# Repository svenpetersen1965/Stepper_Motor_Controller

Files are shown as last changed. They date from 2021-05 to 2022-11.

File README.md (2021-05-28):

# Stepper Motor Controller
The purpose of this project is top provide an Arduino (Pro Micro) based stepper motor controller with two output channels, rotary encoder, LCD display and an RS-232 interface (beside the serial via USB interface of the Pro Micro) with a 3D printed case and a software framework (Arduino Sketch) suitable for many purposes.

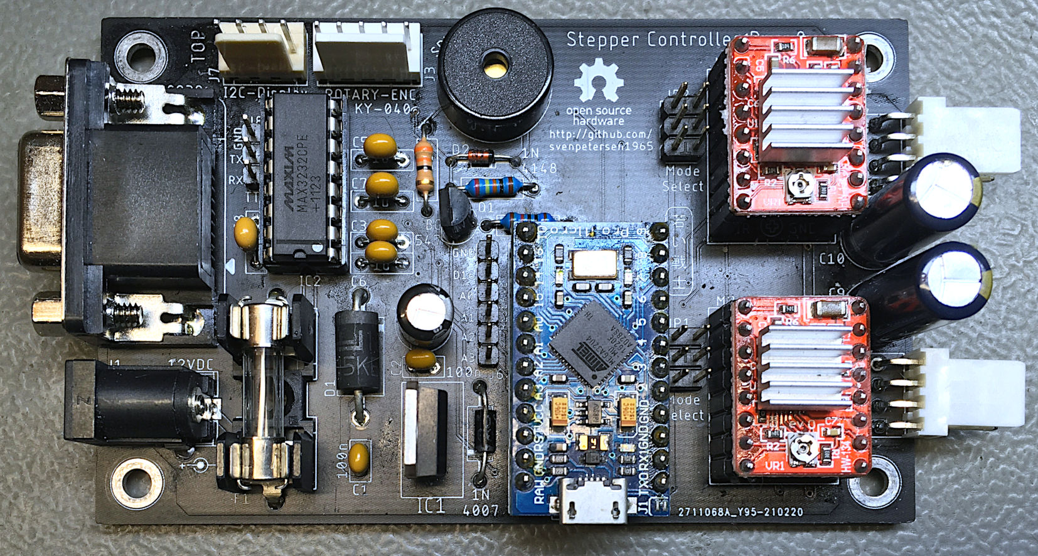
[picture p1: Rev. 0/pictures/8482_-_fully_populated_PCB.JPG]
PCB


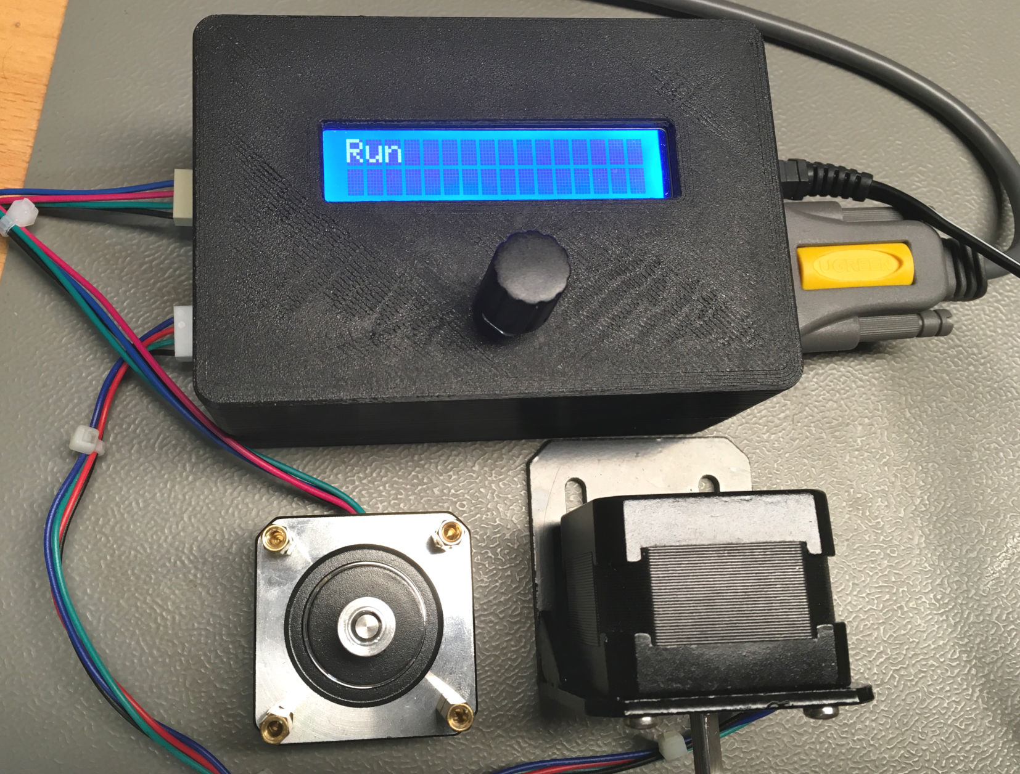
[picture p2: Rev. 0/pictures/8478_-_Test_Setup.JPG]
Setup


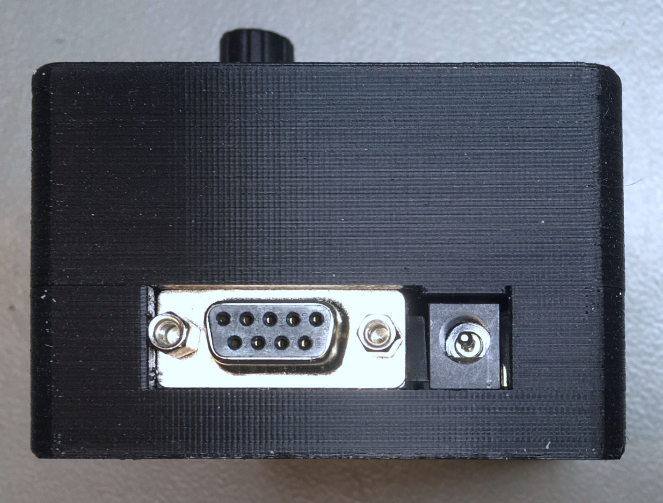
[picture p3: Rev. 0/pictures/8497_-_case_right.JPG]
Power and RS-232


The 3D printed case provides different versions of the top and bottom shells. 

In case you are not experienced with cable making, you might want to read the <a href="http://tech.guitarsite.de/cable_making.html">essay about this topic on my website</a>.

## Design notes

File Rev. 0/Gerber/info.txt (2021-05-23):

      
       Board: Stepper_Controller
       Rev.:  0
  
       Files:
       ======
  
       All Gerber files are generated in extended gerber format (RS274X)
       *.TOP        : Film top copper
       *.BOT        :  -"- bottom copper
       *.STC        :  -"- top soldermask 
       *.STS        :  -"- bottom soldermask
       *.PLC        :  -"- silk screen top
       *.PLC        :  -"- silk screen top
       *.DK         : Drills plated Through (Excellon)
       *.NDK        : Drills not plated Through (Excellon)
       *.OUT        : Board outline

       Board Size:
       ===========
       Length     :   99.0 mm
       Width      :   62.0 mm
       Thickness  :   1.6 mm
       Material   :   FR 4
       Copper     :   35 um
       Surface    :   HASL
       
       Remarks:
       ========
       minimum drill: 0.35mm
       minimum width: 8 mil
       minimum distance: 6 mil

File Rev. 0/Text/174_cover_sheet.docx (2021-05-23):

Project Documentation

Stepper Motor Controller

Project number: 174

Revision: 0

Date: 15.05.2021

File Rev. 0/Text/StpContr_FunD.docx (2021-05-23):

Stepper Motor Controller Rev. 0

Functional Description

J1 is the power supply connector. F1 is the 5x20mm fuse, which might require to be adjusted to the application/stepper motors. D1 is a TVS diode for transient (0voltage spike) suppression. It is calculated for a 12V supply voltage. In case a different supply voltage is desired, a different TVS diode has to be selected.

IC1 is shown as a Traco TRS2-2450 DC/DC converter. Since this is pin compatible to the standard linear regulators, a 7805 can be populated instead of the DC/DC converter, which might be required for higher supply voltages (e.G. 24V for 24V stepper motors).

D3 is a protection when switching off the Stepper motor controller. It helps that the output voltage of IC1 is not much higher than the input voltage (due to charged capacitors).

M1 is a Pro Micro, a popular Atmel Atmega32U4 based micro processor module, which is compatible to the Arduino Leonardo. To send the program/script to the Pro Micro, the USB-B micro connector has to be connected to the PC, the Arduino IDE software is running, the Arduino Leonardo is selected and the proper COM-Port.

IC2 is the level translator for RS-232 (the logic levels of RS-232 are about +/-10V with the MAX232. C3, C5, C6 and C7 are part of the charge pump for generating the required voltages for the IC2. J2 is the RS-232 jack. CTS and RTS are connected as well as DTR, DSR and DCD.

J8 can be used to repurpose the RX and TX pins or for spying the serial traffic at TTL level.

J6 is a pin header for the unused I/O pins of M1. It usually does not require to be populated.

The circuit around Q1 serves as a buzzer amplifier/protection circuit. Actually, an IO-Pin of M1 could drive the buzzer, but the buzzer can act as a high voltage spike generator on a mechanical impact. Thus, the circuit. R1 is the base resistor of Q1, R2 is for current limiting, D2 is kind of a free-wheeling diode, that helps to prevent reverse voltages.

M2 and M3 are the Allegro A4988 based stepper drivers. M2 is for Channel A/Stepper 1 and M3 for Channel B/Stepper 2. C9 and C10 are the buffer capacitors for VMOT, the +12V supply voltage for the stepper motors. JP1 and JP2 configure the micro step mode. All jumpers open mean “full step”. An open jumper is interpreted as a LOW signale by the A4988.

There is one common Enable Signal () for both stepper motors. In case it is LOW, the stepper motors are active and the axis cannot be moved manually. It performs steps in this mode. In case is HIGH, no current flows through the stepper windings and the axis can be moved manually (at least, if the stepper does not have a gear).

J7 is a connector for the I²C-Bus. Usually, a display is connected. Since the I²C is a bus, additional I²C devices can be connected.

J3 is a connector for the rotary encoder. A KY-040 module, which is pretty wide spread and unexpensive can be connected here.

StpContr_FunD.docx 23.05.2021 16:36 Drafted by Sven Petersen Page 2 of 2 Doc.-No.: 174-6-02-00

StpContr_FunD.docx 23.05.2021 16:36 Drafted by Sven Petersen Page 1 of 1 Doc.-No.: 000-6-00-00

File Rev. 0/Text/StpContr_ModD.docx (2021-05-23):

Stepper Motor Controller Rev. 0

Module Description

# Introduction

The Board is a multi-purpose stepper motor controller based on a Pro Micro (Arduino) and up to two (Allegro) A4988 stepper motor driver. The power supply of +12V (basic configuration) is provided via a barrel connector.

The user interface consists of an I²C display, a rotary encoded with integrated button switch and a piezo buzzer. The connectivity is either an RS232 serial interface or the USB serial interface of the Pro Micro.

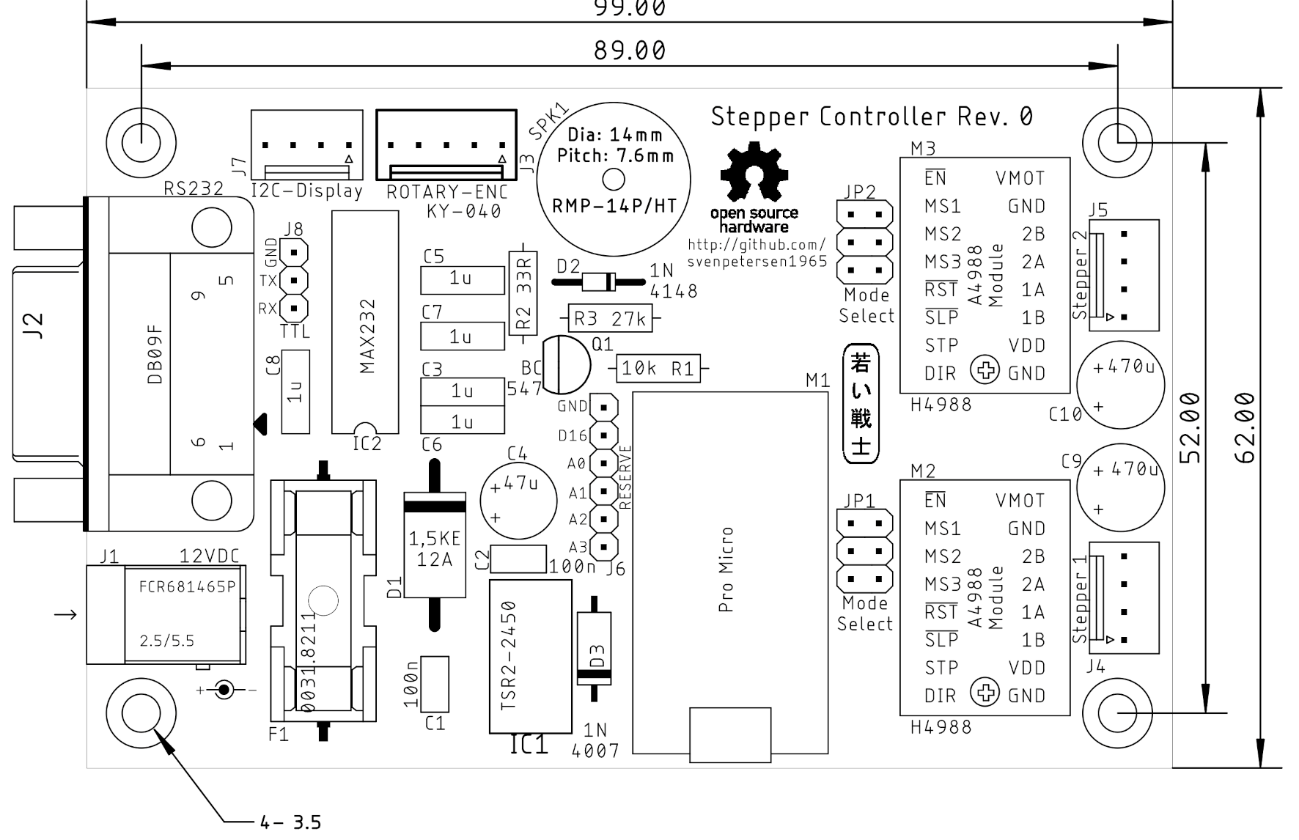
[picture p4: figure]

Figure 1: Dimensions of the Stepper Motor Controller

# Hardware

## The Pro Micro

The Pro Micro is an Arduino Leonardo (Software) compatible, Atmel ATmega32u4-based microprocessor module with 12 digital GPIO pins, 4 analog inputs (which can be used as digital I/Os as well), 32kB Flash, 2.5 kB RAM, 1kB EEPROM and a clock rate of 16MHz and a supply voltage of 5V (3.3V variants with 8MHz are available, but not suitable for this project).

## The A4988 Stepper Driver

The stepper drivers are widely available as modules from Ebay, AliExpress and other online shopping platforms (search term “A4988”). They are based on the Allegro A4988 chip. This chip has five (hardware) selectable step modes: full steps, 1/2, 1/4, 1/8 and 1/16 micro steps. The digital supply voltage is either 5V (used) or 3.3V, the stepper motor supply voltage is up to 35V (12V are used in this projects) and is capable to drive up to 2A.

The micro step mode is selected via jumpers (JP1 for Stepper 1/Channel A and JP2 for Stepper 2/Channel B).

The stepper drivers are controlled by three digital signals:

1. /EN: Enable, active low
2. STEP pulse input
3. DIR direction

The Enable signal /EN needs to be low to activate the driver. A HIGH level will deactivate the drivers. No current flows through the step motor windings, they can be moved freely, stepping will not be executed. The /EN signal of both stepper controllers are interconnected.

A HIGH pulse on the STEP input will result in one (micro) step of the motor in the direction determined by the DIR pin (HIGH = clockwise, LOW = counterclockwise).

Both, the STEP and the DIR signals are separate for each of the two stepper drivers.

There is a small potentiometer on each stepper driver module, which is for adjusting the motor current. To provide approximately equal micro steps, this potentiometer has to be adjusted properly. An adjustment based on the acoustic impression while the stepper motor is running is sufficient for most purposes. It also determines the “hold current”, which influences the supply current and the momentum, the stepper motor is capable to hold.

## The Power Supply

The power supply is connected to a 5mm/2.1mm barrel connector (+12V at the inner contact). The supply voltage is fused and over voltage protected, it is connected to the stepper motor supply pin (VMOT) of the stepper driver. Hence, it is possible to modify the PCB in a way, that 24V stepper motors can be driven. For this purpose, the fuse and the TVS diode D1 need to be modified.

The 5V for supplying the Pro Micro, the digital side of the stepper driver, the display, the buzzer and the rotary encoder, is generated from the input supply voltage. For a +12V supply, a simple linear 7805 voltage regulator is sufficient. The PCB provides the space to install a DC/DC converter (Traco TSR2-2450) instead, that might be required for powering the PCB with a higher supply voltage.

## The Display

The display is connected to the I²C bus via a four-pin connector, which also provides a +5V pin for power supply. This will operate with the wide spread 16 columns/two lines or 20 columns/four lines LCD displays (I²C).

It is of course possible to connect an OLED-display with 5V supply voltage with a suitable software running on the Pro Micro.

## The Rotary Encoder

Rotary encoders with an integrated push button are usually pretty common and suitable for a menu-based mode selection and parameter entry. A widely available rotary encoder module (with on-board pull-up resistors) is the KX-040. The connector for the rotary encoder is adapted to this module. In case, a rotary encoder is not required for the supplication, the pins can be repurposed.

## The Piezo Buzzer

The purpose of the piezo buzzer is providing acoustic feedback or a warning signal for the user. Since piezo elements can produce some nasty voltage spikes when they get bent or beaten, the buzzer is not directly connected to the processor pin, but there is a protection circuit with a transistor and a diode.

## Serial RS-232-Interface

The Pro Micro provides a virtual serial interface via USB for communication and also a real serial interface with RX/TX pins. An RS-232 level driver is integrated on this board. The connector is the D-Sub 9, female, so the stepper controller is a DCE (Data Communication Equipment) like a modem. It connects to a computer (or other DTE = Data Terminal Equipment) via a 1:1 serial cable. Some feedbacks are provided (RTS-DTS and DTR-DRS-DCD).

# Programming

The Stepper Motor Controller (actually the Pro Micro) can be programmed with the Arduino IDE. The following chapters describe the source code of stepper_framework.ino, which does not do anything useful, except testing the hardware, nevertheless, this can be a framework to customized applications.

## Pin Configuration

The pin configuration looks like this:

Pin | Direction | Signal | Purpose
D0 | out | TX | RS-232 Interface serial output
D1 | in | RX | RS-232 Interface serial input
D2 | - | SDA | I²C SDA signal
D3 | - | SCL | I²C SCL signal
D4 | in | ROT_SW | Rotary Encoder Switch
D5 | in | ROT_DATA | Rotary Encoder Data (actually output A)
D6 | out | STP_IN | Stepper driver 1 (Channel A) pulse input
D7 | out | STP_DIR | Stepper driver 1 (Channel A) direction input
D8 | input | ROT_CLK | Rotary Encoder Clock (actually output B)
D9 | out | SND_OUT | Output to the piezo buzzer
D10 | out | | Stepper Enable (active low) for both stepper drivers
D14 | out | STP2_IN | Stepper driver 2 (Channel B) pulse input
D15 | out | STP2_DIR | Stepper driver 2 (Channel B) direction input
D16 | - | D16 | Reserved GPIO
A0 | - | A0 | Reserved (analog) GPIO
A1 | - | A1 | Reserved (analog) GPIO
A2 | - | A2 | Reserved (analog) GPIO
A3 | - | A3 | Reserved (analog) GPIO

## Stepper Driver

The pins are defined like this:

#define step1 6 // stepper 1 step

#define dir1 7 // stepper 1 direction

#define step2 14 // stepper 2 step

#define dir2 15 // stepper 2 direction

#define nstpena 10 // enable both steppers (active low)

Pin initialization:

// setup stepper controller

digitalWrite( step1, LOW ); // LOW -> Step Signal

digitalWrite( dir1, st_direction ); // default direction

digitalWrite( step2, LOW ); // LOW -> Step Signal

digitalWrite( dir2, st_direction ); // default direction

digitalWrite( nstpena, HIGH ); // disable stepper by setting the enable pin HIGH

pinMode( step1, OUTPUT ); // step1 is an output

pinMode( dir1, OUTPUT ); // dir1 is an output

pinMode( step2, OUTPUT ); // step1 is an output

pinMode( dir2, OUTPUT ); // dir1 is an output

pinMode( nstpena, OUTPUT ); // nstpena is an output, that is the enable output for both stepper controllers

Previously, the direction was set to the desired value:

#define step_cw HIGH // for clockwise, the direction pin is HIGH

#define step_ccw LOW // for counterclockwise, the direction pin is LOW

[…]

digitalWrite( dir1, step_cw );

To switch on the stepper driver output and perform a step, the stepper drivers need to be enabled by setting the enable input LOW:

digitalWrite( nstpena, LOW ); // enable stepper controller

Setting the direction:

#define step_cw HIGH // for clockwise, the direction pin is HIGH

#define step_ccw LOW // for counterclockwise, the direction pin is LOW

[…]

digitalWrite( dir1, step_cw );

One step is performed like this:

void makeStepA( void ) { // make a step on motor A

digitalWrite( step1, HIGH );

delayMicroseconds( puls_width );

digitalWrite( step1, LOW );

}

## The Piezo Buzzer

Pin definition:

#define buzzer 9 // buzzer

Pin initialization:

pinMode( buzzer, OUTPUT ); // the buzzer is an output

Using the piezo buzzer:

// beep "hello"

tone( buzzer, 4000 ); // 1kz sound on buzzer

delay( 1000 ); // for 1 second

noTone( buzzer );

## The LCD-Display

The I²C LDC Display requires including two libraries:

#include <Wire.h> // import Wire library

#include <LiquidCrystal_I2C.h> // import LiquidCrystal_I2C library

The initialization includes the I²C address, the number of column and the number of lines. Here a 16x2 display is used.

LiquidCrystal_I2C lcd(0x27, 16, 2); // define the lcd display (i²c address

// 0x27, 16 columns, 2 lines

## The Timer 1 Interrupt

The Timer 1 interrupt is actually the heartbeat of the software. This interrupt occurs periodically and the so called ISR (Interrupt Service Routine) is executed. The cycle duration/periodicity depends on the setup (parameters) of Timer 1.

Note: Many beginners and intermediate programmers are afraid of using interrupts. This fear is actually not required! The ISR can be imagined as a sub routine, that is executed on interrupt, which is not noticed by the main program and can happen at any time. It is a task, that is executed in the background. The communication between the main program and the ISR is accomplished with variables.

There are two main rules for the Interrupt Service Routine:

1. Keep it simple (the execution times should not be too long)
2. The variables, which need to be seen by the main program and the ISR need to be declared as “volatile” to disable compiler optimizations, that might want to store such a variable in a register. The main program will look up the value by loading the register, while the ISR has changed the value in memory.

Rule number 2 is violated quite often, which leads to an unreliable/unpredictable processing of the events, that cause the interrupt.

The declaration of a “volatile” variable looks like this:

volatile boolean step_flag = 0;

It works with all basic variable types. step_flag is set by the ISR (after a defines time has elapsed), the main loop is checking if step_flag is set, if so, a step is performed and step_flag is then reset by the main loop. That simple!

The setup of the timer interrupt looks like this:

/* ==================== TIMER 1 setup ======================= */

// Interrupt every 0.000496 sec (= 2016.13Hz)

// prescaler = 256

// Compare Match Register = 30

cli(); // disable interrupts

// reset timer1

TCCR1A = 0; // set TCCR1A register to 0

TCCR1B = 0; // set TCCR1B register to 0

TCNT1 = 0; // reset counter value

OCR1A = 30; // set compare match register of timer 1

TCCR1B |= (1 << CS12); // 1:256 pre-scaling for timer1

TCCR1B |= (1 << WGM12); // turn on CTC mode

TIMSK1 |= (1 << OCIE1A); // enable timer compare interrupt

sei(); // allow interrupts

The clock frequency is 16MHz for the Pro Micro (5V version). This frequency is divided by the prescaler (here 256). The result is a frequency of 62.5kHz, which is the input frequency of timer 1. The compare/match register is set to 30. So, timer 1 counts from 0 to 30 before the timer interrupt occurs. That are 31 counts.

T_(TIMER1) =(prescaler ∙(OCR1A+1))/(16MHz)=(256∙(30+1))/(16MHz)=0.496msec

CTC mode means the described cyclic counting mode.

The prescaler has a just few specific modes.

CS12 | CS11 | CS10 | Prescaler
0 | 0 | 1 | 1:1 (no prescaler)
0 | 1 | 0 | 1:8
0 | 1 | 1 | 1:64
1 | 0 | 0 | 1:256
1 | 0 | 1 | 1:1024

A recommended reading about the timer interrupts is: https://www.simsso.de/?type=arduino/timer-interrupts

This website includes a parameter calculator.

## The Interrupt Service Routine

The ISR includes the timing for the steps and the processing of the rotary encoder signals.

ISR(TIMER1_COMPA_vect) { // function which will be called
// when an interrupt occurs at timer 1

// ========= every one second ========

if (++t1_ticks == t1_ticks_sec) { // set tick_1s every 2016 IRQ cycles (every 1 second)

tick_1s = 1;

t1_ticks = 0; // reset the tick counter

}

// === count the time before the next stepper step ===

if (++step_ticks == step_duration) {

step_flag = 1;

step_ticks = 0;

}

// ============== rotary encoder =====================

rot_read = digitalRead( rot_clk );

if ( rot_read != rot_clk_status) { // is rot_clk different for
// <debounce> cycles?

if (--rot_clk_debounce == 0) {

rot_clk_status = rot_read; // if yes: change status

}

}

else {

rot_clk_debounce = debounce; // if it is equal -> reset
// the debounce counter

}

if (rot_clk_status != rot_clk_status_old) { // did a status change
// occur?

if (rot_clk_status == LOW) { // is it a falling edge?

if (digitalRead( rot_data ) == LOW) { // yes: set the roraty value
//according to rot_data

rot_value--; // LOW -> CCW

}

else {

rot_value++; // HIGH -> CW

}

}

rot_clk_status_old = rot_clk_status; // update old status

}

rot_read = digitalRead( rot_sw ); // read rot switch

if ( rot_read != rot_sw_status) { // is rot_sw different for
// <debounce> cycles?

if (--rot_sw_debounce == 0) {

rot_sw_status = rot_read; // if yes: change status

}

}

else {

rot_sw_debounce = debounce; // if it is equal -> reset
// the debounce counter

}

if (rot_sw_status != rot_sw_status_old) { // did a status change
// occur?

if (rot_sw_status == LOW) { // is it a falling
// edge?

rot_button = true; // set switch semaphore

}

rot_sw_status_old = rot_sw_status; // update old status

}

}

The ISR consists of three parts:

1. A 1sec tick
2. A tick per desired (micro) step
3. The rotary encoder debouncing and processing (refer to the following chapter)

The 1sec tick is setting the “flag” tick_1s to 1. This flag can be monitored by the main loop. The main loop has to reset this flag after “detection”. This is called a “semaphore”, which means a structure, that is used for signaling between different processes (here it is the ISR and the main loop).

step_flag is the semaphore, which signalizes the main loop, that the time for the next set has elapsed. The main loop has to reset this flag after detection, as well.

## The Rotary Encoder

The rotary encoder part of the ISR (refer to the previous chapter) is supervising the “clock” and the “switch” signals.

The rotary encoded used here has mechanic contacts. Those are bouncing, when they change state. That means they are quickly oscillating for a while, before they finally settle. To detect a valid status change of the rotary encoder, the supervised signal has to stay the same for the debouncing period of time, which is determined be the constant debounce (a certain number of ISR cycles).

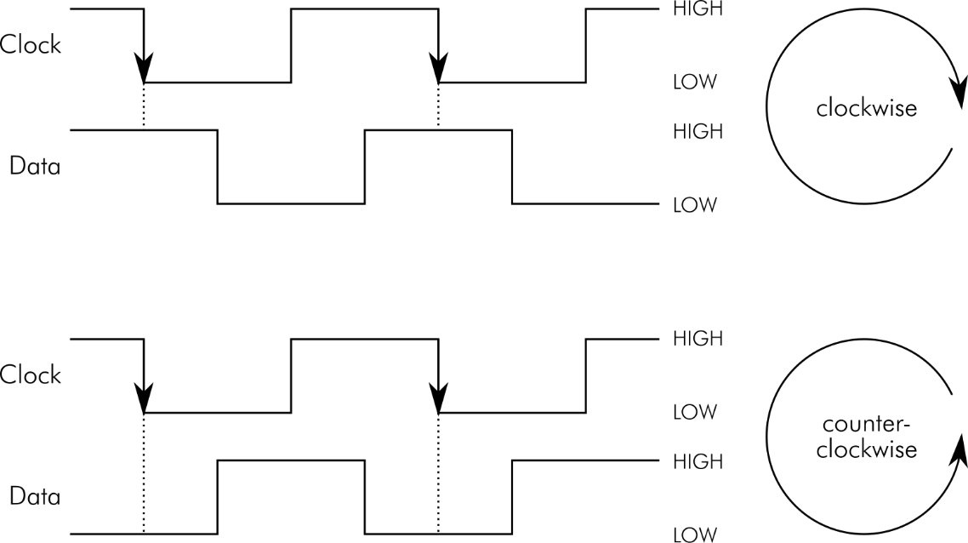
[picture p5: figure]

Figure 2: Operation of the rotary encoder

The relation between the clock and the data signal of the rotary encoder depends on the rotation direction. It is plus or minus a quarter period (that is +/- 90°, 360° is a complete period).

The direction can be detected by reading the data signal right after the falling edge of clock. This is accurate enough for a rotary encoder serving as an input device.

The interrupt service routine (ISR) is detecting a falling edge by comparing the recently read (valid) status of the clock signal (rot_clk_status) and the previously read status (rot_clk_status_old). In case both are different and the present status is LOW, a falling edge is detected. Now, the data signal is read. Depending on the state of the data signal, the variable, that holds the number of rotary encoder clicks (rot_value) is counted up (clockwise turn) or down (counterclockwise turn). rot_value is another semaphore, which is communicating the rotary encoder operation to the main loop.

The status of the rotary encoder’s push button is also monitored by the ISR. Like the clock signal, it has to be debounced. Since the button is a switch to ground (GND), a pushed button shows as reading a LOW state. The (after debouncing) valid state of the button is stored in the semaphore rot_button. The variable is true, if a button push is detected.

Processing the rotary encoder in the main loop is fairly simple. Just the previously mentioned semaphores have to be monitored.

Detecting the button:

lcd.setCursor(14,0);

if (rot_button==true) { // rotary encoder:
// button pushed

rot_button = false; // reset this flag

// after detection

Serial1.print("Button->set (Channel ");

if (stepper == step_cha) {

Serial1.println("A)");

}

else {

Serial1.println("B)");

}

}

Or the direction of rotation:

if (rot_value != 0) {

if (rot_value < 0) {

num_steps = num_steps - 10;

rot_value++;

}

else {

num_steps = num_steps + 10;

rot_value--;

}

lcd.setCursor(7,1);

lcd.print( num_steps );

lcd.print( " " );

Serial1.print( "Steps: " );

Serial1.println( num_steps );

}

Here the number of steps (num_steps) is reduced by 10 on each “click” while rot_value is < 0 (direction = CCW) and increased by 10 while rot_value is > 0 (direction = CW).

## RS-232

Other than the “regular” serial (via USB) interface, this RS-232 is addressed as Serial1 in the Arduino IDE. The programming works like with the first serial interface. The recommended reading is https://www.arduino.cc/reference/en/language/functions/communication/serial/.

The initialization works with

Serial1.begin(9600);// the RS232 interface (RX, TX on pin 0 and 1) is

// Serial1.

This the 9600 bit/s (aka 9600 baud), 8N1 (8 data bits, No parity, 1 stop bit), a very common baud rate and data format.

Sending text via the serial interface is fairly simple:

Serial1.println( "Hello RS-232" ); // say hello

The RS-232 interface is also for receiving commands from a host. To collect this data and later process it (parsing the string = extracting the commands and parameters), some RAM space (a buffer) is allocated. For the parsing, the String functions are required

String recString = ""; // receive command buffer

[…]

recString.reserve(80);

A process, that is executed on every event on the Serial1 (RS-232) interface is

void serialEvent1() {

while (Serial1.available()) { // bytes available on Serial1?

recByte = (char)Serial1.read(); // read it

if (recByte == (char)10) { // is it "new line character"?

recComplete = true; // yes: the line is complete

}

else {

recString += recByte; // no: append character to input string

}

}

}

As long as there is data available on the interface, it is checked, if the data byte (actually a character) is a “Line Feed” (= (char)10 ). The line feed denotes the end of a command string. If so, a semaphore (recComplete) is set true. If it is a different character, this will be appended to the buffer recString.

The parsing of the received string in the main loop looks like this:

if (recComplete) { // a complete command line is received on RS-232

lcd.setCursor(0,1); // position the cursor on the second line

lcd.print( recString ); // print the received string

lcd.print( " " ); // clear the line after that string

recString.toUpperCase(); // convert the line to upper case

// (it is not case sensitive)

syntaxError = false; // reset the Syntax Error flag

if (recString[0] == 'A') { // is the first character an A?

stepper = step_cha; // yes: select Stepper#1 (channel A)

}

else if (recString[0] == 'B') { // is the first character a B?

stepper = step_chb; // yes: select Stepper#2 (channel B)

}

else {

syntaxError = true; // else, the syntax is not correct.

}

if (!syntaxError) { // syntax still correct?

int pos = (int) recString.indexOf(","); // find the first comma ","

if (pos < 1) { // if no comma is found

syntaxError = true; // set the Syntax Error Flag

}

else { // a comma is found:

recString.remove(0,pos+1); // remove the beginning, the comma

// included

num_steps = (int) recString.toInt();// convert the string to

// integer -> num_steps

if (num_steps<0) { // is it a negative number?

num_steps = -num_steps; // yes: make it positive

st_direction = step_ccw; // the direction is counterclockwise

}

else { // no:

st_direction = step_cw; // the direction is clockwise

}

digitalWrite( dir1, st_direction ); // set the direction of both

digitalWrite( dir2, st_direction ); // stepper motors

}

}

if (syntaxError) {

Serial1.println("? SYNTAX ERROR"); // report the syntax error

}

else {

Serial1.print("Execute: Channel "); // report the execution

switch (stepper) {

case step_cha: {

Serial1.print("A, "); // Channel A

break;

}

case step_chb: {

Serial1.print("B, "); // Channel B

break;

}

}

Serial1.print( num_steps ); // and the number of steps

if (st_direction == step_cw) {

Serial1.println(" steps, CW"); // and the direction

}

else {

Serial1.println(" steps, CCW");

}

}

recComplete = false; // reset the semaphore

recString = ""; // reset the recString (receive buffer)

The command line will let the selected stepper motor turn CW or CCW by the sent number of steps.

A proper command line looks like this:

<channel>, <number of steps>

While <channel> is A or B or a or b (it is not case sensitive) and a positive <number of steps> will turn the clockwise and a negative <number of steps> will turn counter clockwise.

## State Machine

The main loop is designed as a (finite-)state machine. This is a very common structure for micro controller software, which is quite useful to know.

Depending on the state, the actions and reactions are different. This (desired) behavior can be depicted in a state diagram (Figure 3).

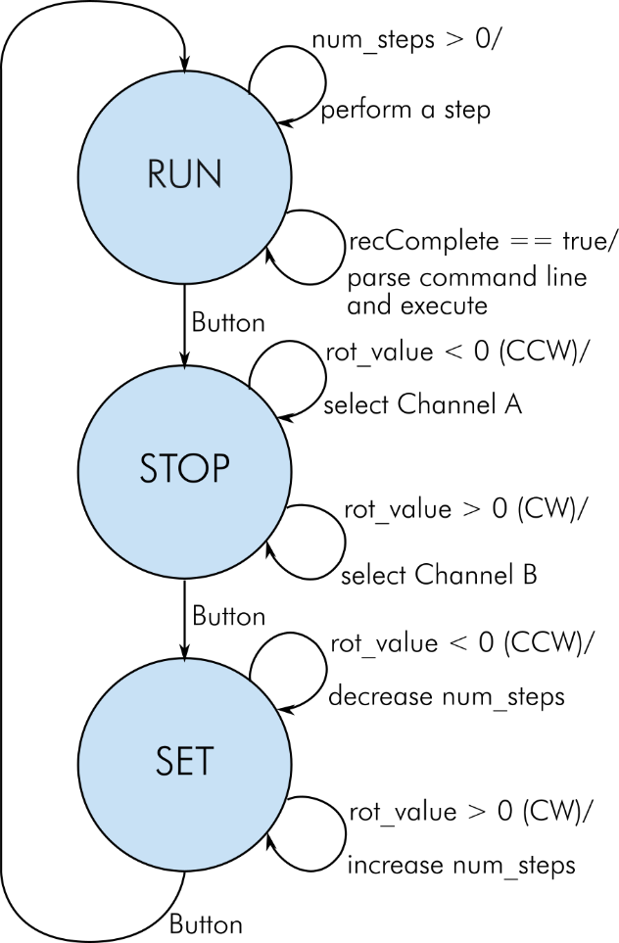
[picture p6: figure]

Figure 3: State diagram

The state machine has three states: RUN, STOP and SET. The states are represented by int values defined like this:

// state machine states

#define sm_stop // assigning a numbers to the state machine states

#define sm_set 1

#define sm_run 2

The state RUN is entered first, it checks, if num_steps is greater 0, if so, it performs a step and decreases num_steps by one.

Also, it checks, if a command line (via RS-232) is complete (recComplete is true), if so, the command line is parsed and executed.

In case the push button of the rotary encoder is pressed, it enters the state STOP.

The state STOP watches the rotary encoder. If it is turned counterclockwise, Stepper channel A is selected, if it is clockwise, Stepper channel B is selected.

If the push button is pushed, the state SET becomes active.

While SET the number of steps to perform next and the direction is adjusted. If the rotary encoder is turned clockwise, the variable num_steps is increased by 10, while counterclockwise, num_steps is increased by 10. A negative number will select counterclockwise for both stepper motors. Pressing the push button will enter the state RUN.

The over-all structure of the state machine is a switch/case construction in the main loop.

switch (state_machine) {

case sm_stop : {

[…]

break;

}

case sm_set : {

[…]

break;

}

case sm_run : {

[…]

break;

}

}

# Connector Pinouts

## J1 - Power Connector

J1 is a 2.5mm/5.5mm barrel jack.

Pin | Signal
Inner | +12VDC
Outer | GND

## J2 – RS-232 Serial Interface

D-Sub, 9 pins, female

Pin | Signal | Note
1 | DCD | Feedback DCD – DTR - DSR
2 | RxD | Output
3 | TxD | Input
4 | DTR | Feedback DCD – DTR – DSR
5 | GND | Ground
6 | DSR | Feedback DCD – DTR – DSR
7 | RTS | Feedback RTS - CTS
8 | CTS | Feedback RTS – CTS
9 | RI | Not connected

## J3 – Rotary Encoder

KF2510 series, 5pin (or Molex P/N 22272051) – vertical header with friction lock. Pinout for KY-040 rotary encoder module.

Pin | Signal | Note
1 | GND
2 | +5V
3 | Switch | Button
4 | Data | Actually, Channel A
5 | Clock | Actually, Channel B

The counterpart of J3 is a crimp housing (also KF2510 series, which is wide spread on Ebay, AliExpress and other online shops) and fitting crimp terminals. Alternatively, Molex P/N 22013047 and crimp terminal P/N 0850-0114 can be used.

## J4, J5 – Stepper Motor Outputs

KF2510 series, 4pin (or Molex P/N 22272041) – vertical header with friction lock or horizontal (90°) Molex P/N 22057048. J4 is Channel A/Stepper 1, J5 is Channel B/Stepper 2.

Pin | Signal | Note
1 | 1B | stepper motor blue cable
2 | 1A | stepper motor red cable
3 | 2A | stepper motor green cable
4 | 2B | stepper motor black cable

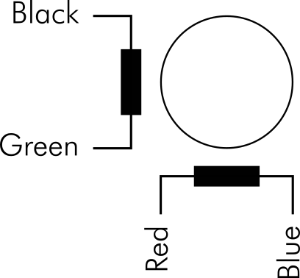
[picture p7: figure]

Figure 4: Windings of the stepper motor/cable colors

## J6 – Reserved I/O-Pins

The free GPIO-Pins of the Pro Micro are connected to a pin header (6 pins, 2.54mm pitch) which does not require to be placed. These pins might serve for connecting sensors/switches/actors

Pin | Signal | Note
1 | GND
2 | D16 | GPIO D16, PCINT2
3 | A0 | Analog input/GPIO
4 | A1 | Analog input/GPIO
5 | A2 | Analog input/GPIO
6 | A3 | Analog input/GPIO

## J7 – I²C/Display Connector

KF2510 series, 4pin (or Molex P/N 22272041) – vertical header with friction lock. Pinout for LCD Displays (16x2) with I²C controller.

Pin | Signal | Note
1 | SCL | I²C clock
2 | SDA | I²C data
3 | +5V
4 | GND

The counterpart of J7 is a crimp housing (also KF2510 series, which is wide spread on Ebay, AliExpress and other online shops) and fitting crimp terminals. Alternatively, Molex P/N 22012041 and crimp terminal P/N 0850-0114 can be used.

## J8 – TX/RX Reserve Header

The TX and RX signals are routed to a pin header (3 pins, 2.54mm), which is not placed, in case it is desired to repurpose them or to watch the data exchange on the serial port/RS-232.

Pin | Signal | Note
1 | GND
2 | TX | serial output, GPIO D1
3 | RX | serial input, GPIO D2

# Jumpers

There are two jumpers, JP1 and JP2. Both serve the setting of the step modes (full step, ½ step, ¼ step, 1/8 step and 1/16 step). JP1 determines the mode of stepper #1/channel A, JP2 does so for stepper#2/channel B).

MS1 / JPx 1-2 | MS2 / JPx 3-4 | MS3 / JPx 5-6 | Mode/micro step resolution
L/open | L/open | L/open | Full Step
H/set | L/open | L/open | Half Step
L/open | H/set | L/open | Quarter Step
H/set | H/set | L/open | Eighth Step
H/set | H/set | H/set | Sixteenth Step

The footprints of the jumpers allow fix solder bridges instead of a pin header and jumper.

# Assembly

## The PCB

The PCB can be fully populated or some not requires parts can be omitted.

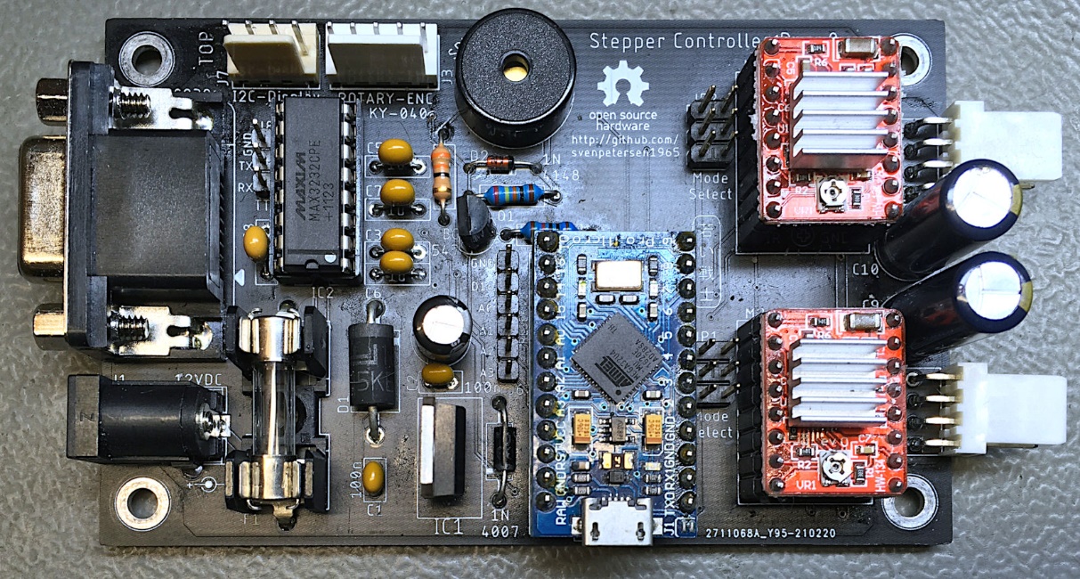
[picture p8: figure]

Figure 5: Fully populated PCB

Requirement | Components
Always populate | J1, F1, C1, C2, C4, D3, M1, M2, C9, J4
2nd stepper controller | M3, C10, J5
Buzzer | R1, R1, R2, R3, D2, SPK1
Display | J7
Rotary Encode | J3
RS-232 | J2, IC2, C3, C5, C6, C7, C8
Micro steps required and jumpered | Channel A: JP1, Channel B: JP2. A fix setting of the jumpers can be accomplished with solder bridges
Do not place (until required) | J6, J8

## Cables

In case the 90° pin headers are used for the stepper motor connection (J4, J5), there are only two cables required:

1. the display cable
2. the rotary encoder cable

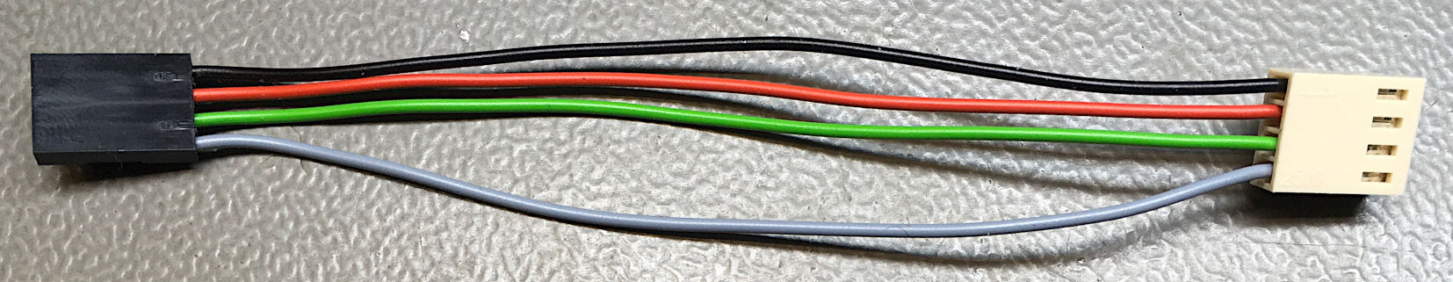
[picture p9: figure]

Figure 6: The display (I²C) cable

This display cable consists of the following components:

Pos. | Qty | Part
1 | 1 | DuPont crimp housing, 4 pins
2 | 4 | DuPont crimp terminals
3 | 14cm | Cable, 0.25mm²/AWG24, black
4 | 14cm | Cable, 0.25mm²/AWG24, red
5 | 14cm | Cable, 0.25mm²/AWG24, green
6 | 14cm | Cable, 0.25mm²/AWG24, grey
7 | 4 | KF2510 crimp terminals
8 | 1 | KF2510 crimp housing, 4 pins

The colors of the cables are a suggestion only.

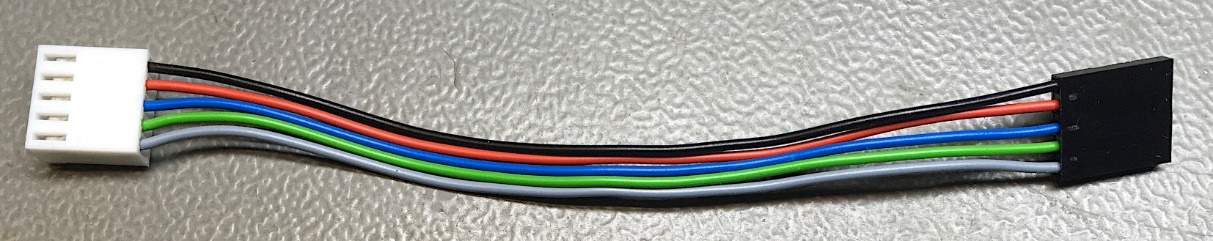
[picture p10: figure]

Figure 7: Rotary encoder cable

This rotary encoder cable consists of the following components:

Pos. | Qty | Part
1 | 1 | DuPont crimp housing, 5 pins
2 | 5 | DuPont crimp terminals
3 | 14cm | Cable, 0.25mm²/AWG24, black
4 | 14cm | Cable, 0.25mm²/AWG24, red
5 | 14cm | Cable, 0.25mm²/AWG24, blue
6 | 14cm | Cable, 0.25mm²/AWG24, green
7 | 14cm | Cable, 0.25mm²/AWG24, grey
8 | 5 | KF2510 crimp terminals
9 | 1 | KF2510 crimp housing, 5 pins

Optionally, a DIN connector can be used for the stepper motor connections.

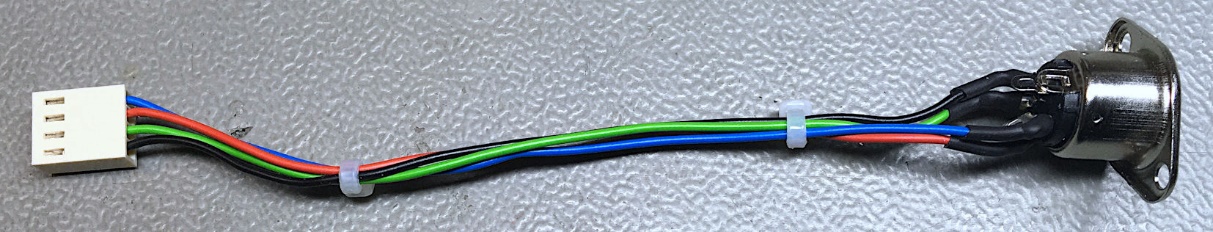
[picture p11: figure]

Figure 8: Stepper cable (internal, optional)

Pos. | Qty | Part
1 | 1 | DIN Jack, 5 pins (e.g. Reichelt MAB 5S)
2 | 14cm | Cable, 0.25mm²/AWG24, black
3 | 14cm | Cable, 0.25mm²/AWG24, green
4 | 14cm | Cable, 0.25mm²/AWG24, red
5 | 14cm | Cable, 0.25mm²/AWG24, blue
6 | 5 | KF2510 crimp terminals
7 | 1 | KF2510 crimp housing, 5 pins
8 | 6cm | Shrinkable sleeve (2.4/1.2)

## 3D Printed Case

It is recommended to use the 3D printed case for this project. It consists of a top and a bottom shell and is constructed in Fusion 360. The STL files for 3D printing are provided as well as the Fusion 360 project.

The display is attached with 4 screws (C2.9x6.5 DIN 7981 recommended). The rotary encoder is attached with the nut included in it. The cables should be connected prior to mounting those components.

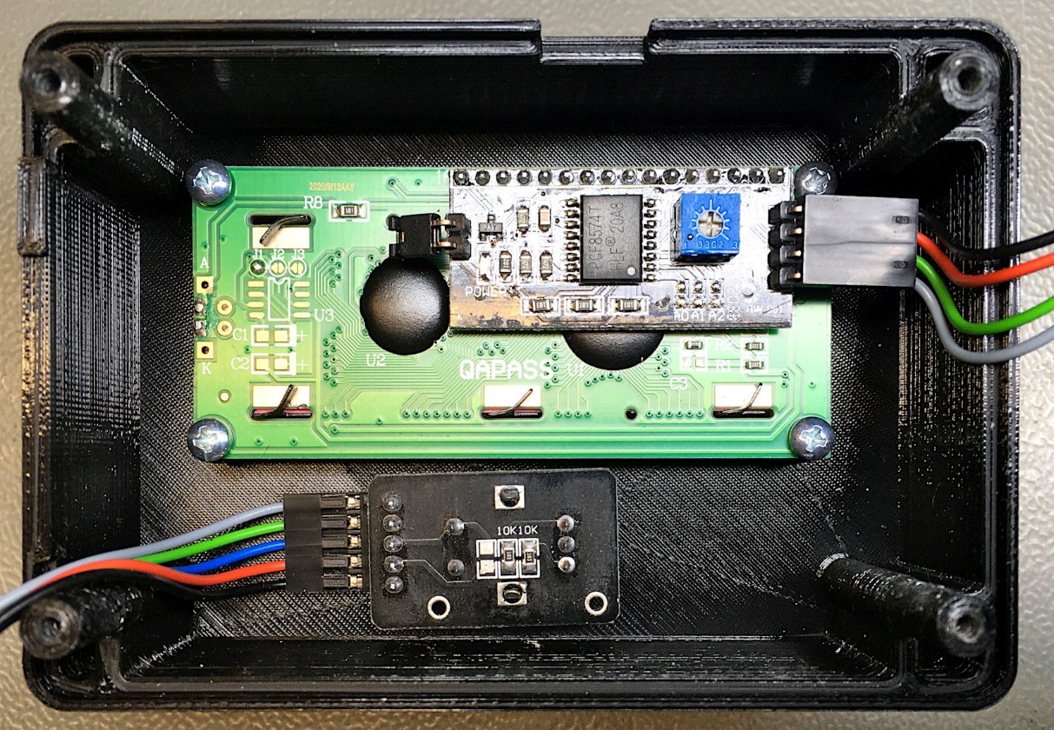
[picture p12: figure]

Figure 9: Top shell with mounted LCD display and rotary encoder KY-040

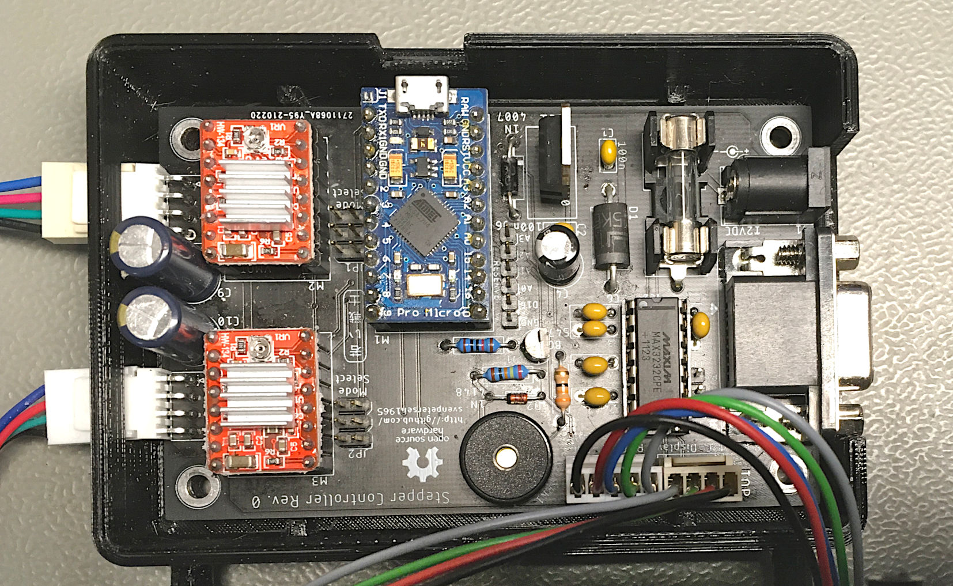
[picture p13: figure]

Figure 10: PCB in bottom shell

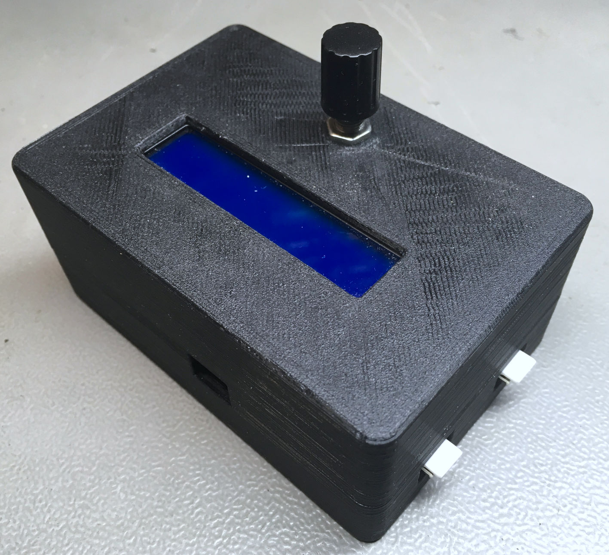
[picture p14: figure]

Figure 11: Case from top, left

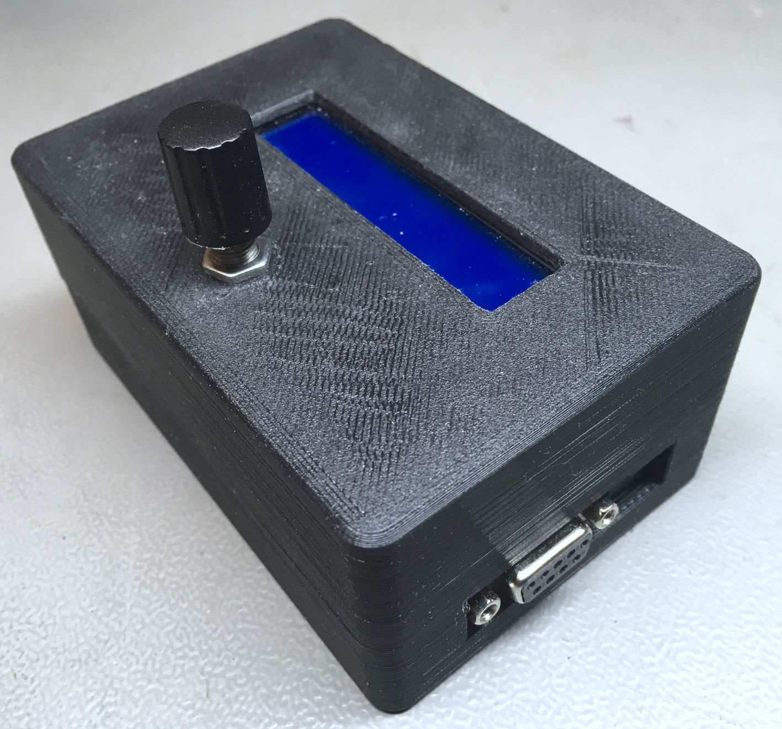
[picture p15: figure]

Figure 12: case from bottom, right

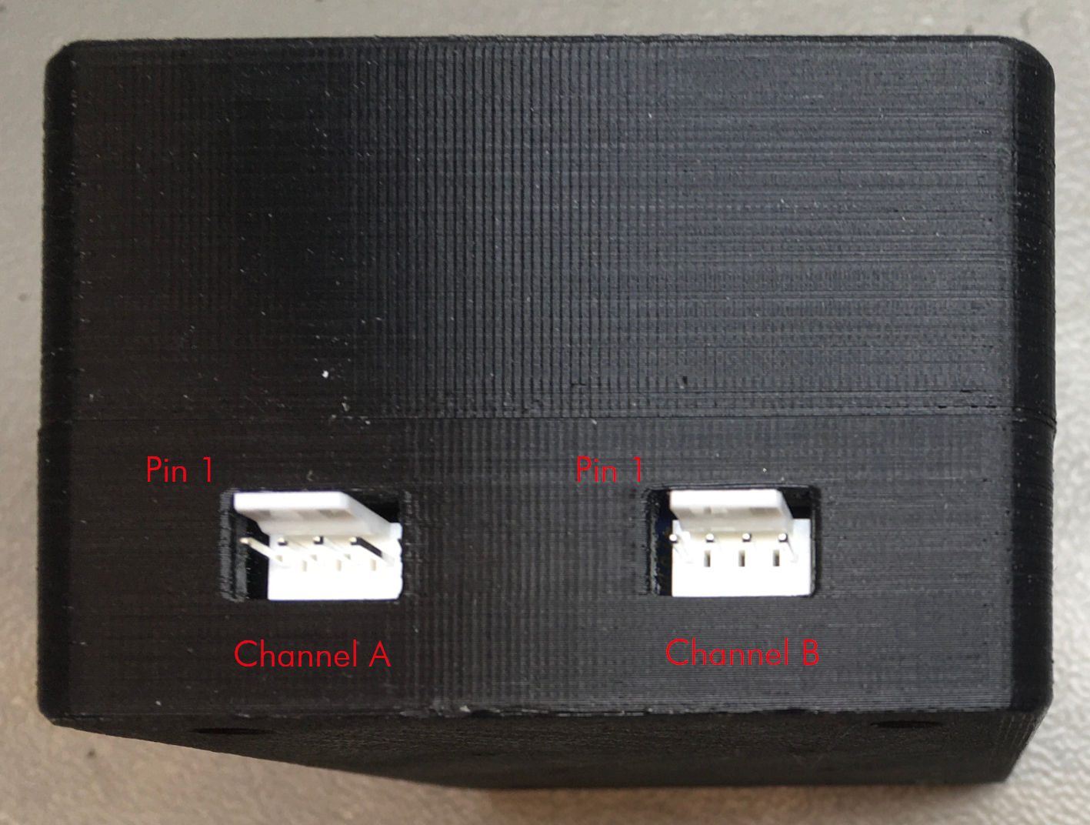
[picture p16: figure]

Figure 13: left side


Figure 14: right side

There are different versions of the top and bottom shell provided. The top shell can have a mounting space for a DIN connector (that could serve as a stepper motor connector), the bottom shell can have the cut outs for the 90° stepper motor connector as shown in Figure 10.

For closing the case, with 4 screws (C2.9x13 DIN 7981 recommended) are required.

# Revision History

## Rev. 0

- Fully functional prototype

StpContr_ModD.docx 23.05.2021 16:35 Drafted by Sven Petersen Page 2 of 2 Doc.-No.: 174-6-01-00

StpContr_ModD.docx 23.05.2021 16:35 Drafted by Sven Petersen Page 1 of 1 Doc.-No.: 000-6-00-00

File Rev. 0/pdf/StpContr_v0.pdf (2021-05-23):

# Project Documentation

## Stepper Motor Controller

## Project number: 174

## Revision: 0

## Date: 15.05.2021

StpContr_ModD.docx | | 23.05.2021 16:35
Drafted by Sven Petersen | Page 1 of 22 | Doc.-No.: 174-6-01-00

### Stepper Motor Controller Rev. 0

### Module Description

Table of Contents

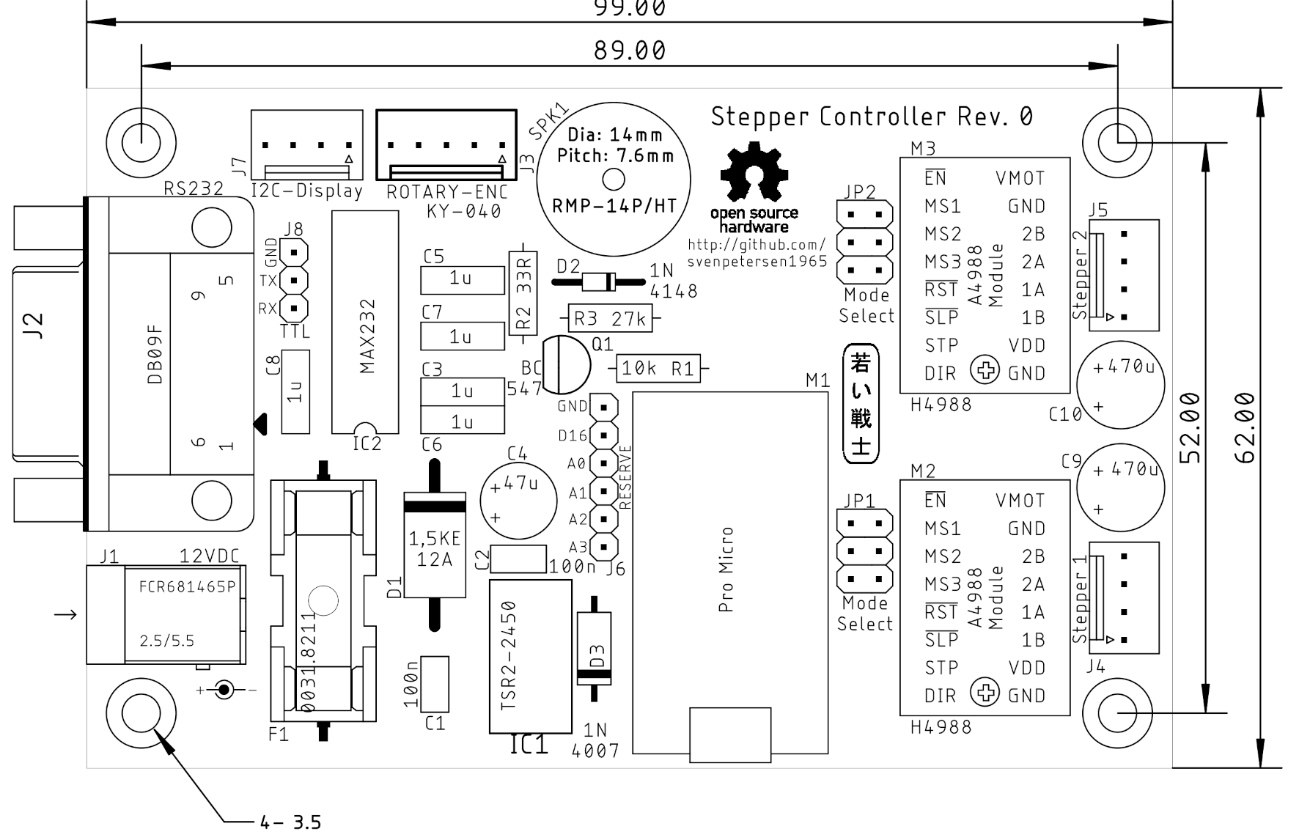
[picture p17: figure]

Drafted by Sven Petersen | Page 2 of 22 | Doc.-No.: 174-6-01-00

## Introduction

The Board is a multi-purpose stepper motor controller based on a Pro Micro (Arduino) and up to two (Allegro) A4988 stepper motor driver. The power supply of +12V (basic configuration) is provided via a barrel connector.

The user interface consists of an I²C display, a rotary encoded with integrated button switch and a piezo buzzer. The connectivity is either an RS232 serial interface or the USB serial interface of the Pro Micro.

Figure 1: Dimensions of the Stepper Motor Controller

## Hardware

### The Pro Micro

The Pro Micro is an Arduino Leonardo (Software) compatible, Atmel ATmega32u4-based microprocessor module with 12 digital GPIO pins, 4 analog inputs (which can be used as digital I/Os as well), 32kB Flash, 2.5 kB RAM, 1kB EEPROM and a clock rate of 16MHz and a supply voltage of 5V (3.3V variants with 8MHz are available, but not suitable for this project).

### The A4988 Stepper Driver

The stepper drivers are widely available as modules from Ebay, AliExpress and other online shopping platforms (search term “A4988”). They are based on the Allegro A4988 chip. This chip has five (hardware) selectable step modes: full steps, 1/2, 1/4, 1/8 and 1/16 micro steps. The digital supply voltage is either 5V (used) or 3.3V, the stepper motor supply voltage is up to 35V (12V are used in this projects) and is capable to drive up to 2A.

Drafted by Sven Petersen | Page 3 of 22 | Doc.-No.: 174-6-01-00

The micro step mode is selected via jumpers (JP1 for Stepper 1/Channel A and JP2 for Stepper 2/Channel B).

The stepper drivers are controlled by three digital signals:

1. /EN: Enable, active low

### 2. STEP pulse input 3. DIR direction

The Enable signal /EN needs to be low to activate the driver. A HIGH level will deactivate the drivers. No current flows through the step motor windings, they can be moved freely, stepping will not be executed. The /EN signal of both stepper controllers are interconnected.

A HIGH pulse on the STEP input will result in one (micro) step of the motor in the direction determined by the DIR pin (HIGH = clockwise, LOW = counterclockwise).

Both, the STEP and the DIR signals are separate for each of the two stepper drivers.

There is a small potentiometer on each stepper driver module, which is for adjusting the motor current. To provide approximately equal micro steps, this potentiometer has to be adjusted properly. An adjustment based on the acoustic impression while the stepper motor is running is sufficient for
most purposes. It also determines the “hold current”, which influences the supply current and the
momentum, the stepper motor is capable to hold.

### The Power Supply

The power supply is connected to a 5mm/2.1mm barrel connector (+12V at the inner contact). The supply voltage is fused and over voltage protected, it is connected to the stepper motor supply pin (VMOT) of the stepper driver. Hence, it is possible to modify the PCB in a way, that 24V stepper motors can be driven. For this purpose, the fuse and the TVS diode D1 need to be modified.

The 5V for supplying the Pro Micro, the digital side of the stepper driver, the display, the buzzer and the rotary encoder, is generated from the input supply voltage. For a +12V supply, a simple linear 7805 voltage regulator is sufficient. The PCB provides the space to install a DC/DC converter (Traco TSR2-2450) instead, that might be required for powering the PCB with a higher supply voltage.

### The Display

The display is connected to the I²C bus via a four-pin connector, which also provides a +5V pin for power supply. This will operate with the wide spread 16 columns/two lines or 20 columns/four lines LCD displays (I²C).

It is of course possible to connect an OLED-display with 5V supply voltage with a suitable software running on the Pro Micro.

### The Rotary Encoder

Rotary encoders with an integrated push button are usually pretty common and suitable for a menu-based mode selection and parameter entry. A widely available rotary encoder module (with on-board pull-up resistors) is the KX-040. The connector for the rotary encoder is adapted to this module. In case, a rotary encoder is not required for the supplication, the pins can be repurposed.

### The Piezo Buzzer

The purpose of the piezo buzzer is providing acoustic feedback or a warning signal for the user. Since piezo elements can produce some nasty voltage spikes when they get bent or beaten, the buzzer is not directly connected to the processor pin, but there is a protection circuit with a transistor and a diode.

Drafted by Sven Petersen | Page 4 of 22 | Doc.-No.: 174-6-01-00

### Serial RS-232-Interface

The Pro Micro provides a virtual serial interface via USB for communication and also a real serial interface with RX/TX pins. An RS-232 level driver is integrated on this board. The connector is the D-Sub 9, female, so the stepper controller is a DCE (Data Communication Equipment) like a modem. It connects to a computer (or other DTE = Data Terminal Equipment) via a 1:1 serial cable. Some feedbacks are provided (RTS-DTS and DTR-DRS-DCD).

## Programming

The Stepper Motor Controller (actually the Pro Micro) can be programmed with the Arduino IDE. The following chapters describe the source code of stepper_framework.ino, which does not do anything useful, except testing the hardware, nevertheless, this can be a framework to customized applications.

### Pin Configuration

The pin configuration looks like this:

Pin | Direction | Signal | Purpose
D0 | out | TX | RS-232 Interface serial output
D1 | in | RX | RS-232 Interface serial input
D2 | - | SDA | I²C SDA signal
D3 | - | SCL | I²C SCL signal
D4 | in | ROT_SW | Rotary Encoder Switch
D5 | in | ROT_DATA | Rotary Encoder Data (actually output A)
D6 | out | STP_IN | Stepper driver 1 (Channel A) pulse input
D7 | out | STP_DIR | Stepper driver 1 (Channel A) direction input
D8 | input | ROT_CLK | Rotary Encoder Clock (actually output B)
D9 | out | SND_OUT | Output to the piezo buzzer
D10 | out | STP_EN | Stepper Enable (active low) for both stepper drivers
D14 | out | STP2_IN | Stepper driver 2 (Channel B) pulse input
D15 | out | STP2_DIR | Stepper driver 2 (Channel B) direction input
D16 | - | D16 | Reserved GPIO
A0 | - | A0 | Reserved (analog) GPIO
A1 | - | A1 | Reserved (analog) GPIO
A2 | - | A2 | Reserved (analog) GPIO
A3 | - | A3 | Reserved (analog) GPIO

### Stepper Driver

The pins are defined like this:

#define step1 6 | // stepper 1 step

#define dir1 7 | // stepper 1 direction

#define step2 14 | // stepper 2 step

#define dir2 15 | // stepper 2 direction

#define nstpena 10 | // enable both steppers (active low)

Pin initialization:

// setup stepper controller
digitalWrite( step1, LOW ); | // LOW -> Step Signal
digitalWrite( dir1, | st_direction | ); | // default direction
digitalWrite( step2, LOW ); | // LOW -> Step Signal

Drafted by Sven Petersen | Page 5 of 22 | Doc.-No.: 174-6-01-00
digitalWrite( dir2, st_direction ); | // default direction

digitalWrite( nstpena, HIGH ); // disable stepper by setting the enable pin HIGH

pinMode( step1, OUTPUT ); | // step1 is an output
pinMode( dir1, OUTPUT ); | // dir1 is an output
pinMode( step2, OUTPUT ); | // step1 is an output
pinMode( dir2, OUTPUT ); | // dir1 is an output
pinMode( nstpena, OUTPUT ); | // nstpena is an output, that is the
enable output for both stepper controllers

Previously, the direction was set to the desired value:

#define step_cw HIGH | // for clockwise, the direction pin is HIGH

#define step_ccw LOW | // for counterclockwise, the direction pin is LOW

[…]
digitalWrite( dir1, | step_cw | );

To switch on the stepper driver output and perform a step, the stepper drivers need to be enabled by setting the enable input LOW:

digitalWrite( nstpena, LOW ); // enable stepper controller

Setting the direction:

#define step_cw HIGH | // for clockwise, the direction pin is HIGH

#define step_ccw LOW | // for counterclockwise, the direction pin is LOW

[…]
digitalWrite( dir1, | step_cw | );

One step is performed like this:

void makeStepA( void ) { | // make a step on motor A
digitalWrite( step1, HIGH );
delayMicroseconds( puls_width );
digitalWrite( step1, LOW );
}

### The Piezo Buzzer

Pin definition:

#define buzzer 9 | // buzzer

Pin initialization:

pinMode( buzzer, OUTPUT ); | // the buzzer is an output

Using the piezo buzzer:

// beep "hello"
tone( buzzer, 4000 ); | // 1kz sound on buzzer
delay( 1000 ); | // for 1 second
noTone( buzzer );

### The LCD-Display

The I²C LDC Display requires including two libraries:

#include <Wire.h> | // import Wire library

Drafted by Sven Petersen | Page 6 of 22 | Doc.-No.: 174-6-01-00
#include <LiquidCrystal_I2C.h> | // import LiquidCrystal_I2C library

The initialization includes the I²C address, the number of column and the number of lines. Here a 16x2 display is used.

LiquidCrystal_I2C lcd(0x27, 16, 2); // define the lcd display (i²c address
// 0x27, 16 columns, 2 lines

### The Timer 1 Interrupt

The Timer 1 interrupt is actually the heartbeat of the software. This interrupt occurs periodically and the so called ISR (Interrupt Service Routine) is executed. The cycle duration/periodicity depends on the setup (parameters) of Timer 1.

Note: Many beginners and intermediate programmers are afraid of using interrupts. This fear is actually not required! The ISR can be imagined as a sub routine, that is executed on interrupt, which is not noticed by the main program and can happen at any time. It is a task, that is executed in the background. The communication between the main program and the ISR is accomplished with variables.

There are two main rules for the Interrupt Service Routine:

### 1. Keep it simple (the execution times should not be too long)

2. The variables, which need to be seen by the main program and the ISR need to be declared
as “volatile” to disable compiler optimizations, that might want to store such a variable in a
register. The main program will look up the value by loading the register, while the ISR has changed the value in memory.

Rule number 2 is violated quite often, which leads to an unreliable/unpredictable processing of the events, that cause the interrupt.

### The declaration of a “volatile” variable looks like this:

volatile boolean step_flag = 0;

It works with all basic variable types. step_flag is set by the ISR (after a defines time has elapsed), the main loop is checking if step_flag is set, if so, a step is performed and step_flag is then reset by the main loop. That simple!

The setup of the timer interrupt looks like this:

/* ==================== TIMER 1 setup ======================= */ // Interrupt every 0.000496 sec (= 2016.13Hz)
// prescaler = 256
// Compare Match Register = 30

cli(); // disable interrupts
// reset timer1
TCCR1A = 0; | // set TCCR1A register to 0
TCCR1B = 0; | // set TCCR1B register to 0
TCNT1 | = 0; | // reset counter value
OCR1A = 30; | // set compare match register of timer 1
TCCR1B |= (1 << CS12); | // 1:256 pre-scaling for timer1
TCCR1B |= (1 << WGM12); | // turn on CTC mode

Drafted by Sven Petersen | Page 7 of 22 | Doc.-No.: 174-6-01-00
TIMSK1 |= (1 << OCIE1A); | // enable timer compare interrupt
sei(); | // allow interrupts

The clock frequency is 16MHz for the Pro Micro (5V version). This frequency is divided by the prescaler (here 256). The result is a frequency of 62.5kHz, which is the input frequency of timer 1. The compare/match register is set to 30. So, timer 1 counts from 0 to 30 before the timer interrupt occurs. That are 31 counts.

# TTIMER1 =

# prescaler ∙ (OCR1A + 1) 16MHz =

256 ∙ (30 + 1)

# 16MHz = 0.496msec

CTC mode means the described cyclic counting mode.

The prescaler has a just few specific modes.

CS12 CS11 CS10 Prescaler
0 | 0 | 1 | 1:1 (no prescaler)
0 | 1 | 0 | 1:8
0 | 1 | 1 | 1:64
1 | 0 | 0 | 1:256
1 | 0 | 1 | 1:1024

A recommended reading about the timer interrupts is: https://www.simsso.de/?type=arduino/timer-interrupts

This website includes a parameter calculator.

### The Interrupt Service Routine

The ISR includes the timing for the steps and the processing of the rotary encoder signals.

ISR(TIMER1_COMPA_vect) { | // function which will be called
// when an interrupt occurs at timer 1 // ========= every one second ========
if (++t1_ticks == t1_ticks_sec) { // set tick_1s every 2016 IRQ cycles (every 1 second)
tick_1s = 1;
t1_ticks = 0; | // reset the tick counter
}

// === count the time before the next stepper step ===
if (++step_ticks == step_duration) {
step_flag = 1;
step_ticks = 0;
}

// ============== rotary encoder =====================
rot_read = digitalRead( rot_clk );
if ( rot_read != rot_clk_status) { | // is rot_clk different for
// <debounce> cycles?
if (--rot_clk_debounce == 0) {
rot_clk_status = rot_read; | // if yes: change status
}
}
else {
rot_clk_debounce = debounce; | // if it is equal -> reset
// the debounce counter

Drafted by Sven Petersen | Page 8 of 22 | Doc.-No.: 174-6-01-00

}
if (rot_clk_status != rot_clk_status_old) { // did a status change
// occur?
if (rot_clk_status == LOW) { | // is it a falling edge?
if (digitalRead( rot_data ) == LOW) { // yes: set the roraty value
| //according to rot_data
rot_value--; | // LOW -> CCW
}
else {
rot_value++; | // HIGH -> CW
}
}
rot_clk_status_old = rot_clk_status; | // update old status
}
rot_read = digitalRead( rot_sw ); | // read rot switch
if ( rot_read != rot_sw_status) { | // is rot_sw different for
| // <debounce> cycles?
if (--rot_sw_debounce == 0) {
rot_sw_status = rot_read; | // if yes: change status
}
}
else {
rot_sw_debounce = debounce; | // if it is equal -> reset
| // the debounce counter
}
if (rot_sw_status != rot_sw_status_old) { | // did a status change
| // occur?
if (rot_sw_status == LOW) { | // is it a falling
| // edge?
rot_button = true; | // set switch semaphore
}
rot_sw_status_old = rot_sw_status; | // update old status
}
}

The ISR consists of three parts:

### 1. A 1sec tick 2. A tick per desired (micro) step 3. The rotary encoder debouncing and processing (refer to the following chapter)

The 1sec tick is setting the “flag” tick_1s to 1. This flag can be monitored by the main loop. The
main loop has to reset this flag after “detection”. This is called a “semaphore”, which means a
structure, that is used for signaling between different processes (here it is the ISR and the main loop).

step_flag is the semaphore, which signalizes the main loop, that the time for the next set has elapsed. The main loop has to reset this flag after detection, as well.

### The Rotary Encoder

The rotary encoder part of the ISR (refer to the previous chapter) is supervising the “clock” and the
“switch” signals.

The rotary encoded used here has mechanic contacts. Those are bouncing, when they change state. That means they are quickly oscillating for a while, before they finally settle. To detect a valid status change of the rotary encoder, the supervised signal has to stay the same for the debouncing period of time, which is determined be the constant debounce (a certain number of ISR cycles).

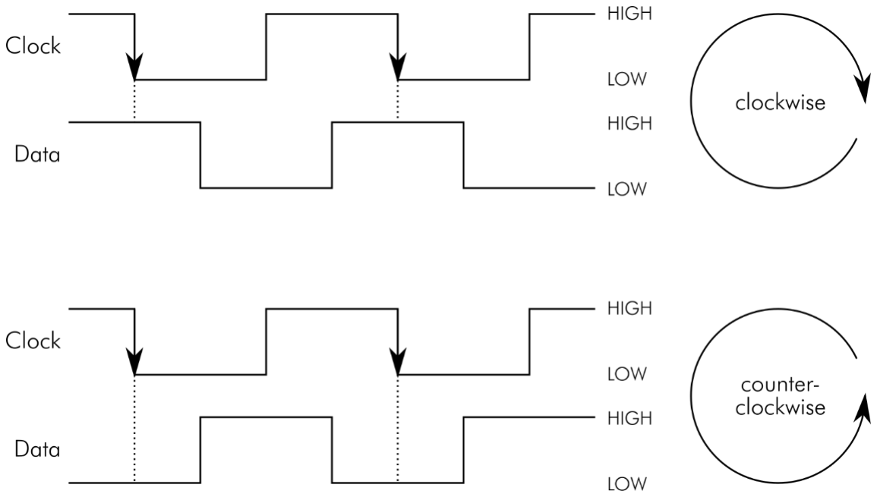
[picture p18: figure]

Drafted by Sven Petersen | Page 9 of 22 | Doc.-No.: 174-6-01-00

Figure 2: Operation of the rotary encoder

The relation between the clock and the data signal of the rotary encoder depends on the rotation direction. It is plus or minus a quarter period (that is +/- 90°, 360° is a complete period).

The direction can be detected by reading the data signal right after the falling edge of clock. This is accurate enough for a rotary encoder serving as an input device.

The interrupt service routine (ISR) is detecting a falling edge by comparing the recently read (valid)
status | of | the | clock | signal | (rot_clk_status) | and | the | previously | read | status
(rot_clk_status_old). In case both are different and the present status is LOW, a falling edge is detected. Now, the data signal is read. Depending on the state of the data signal, the variable, that holds the number of rotary encoder clicks (rot_value) is counted up (clockwise turn) or down (counterclockwise turn). rot_value is another semaphore, which is communicating the rotary encoder operation to the main loop.
The status of the rotary encoder’s push button is also monitored by the ISR. Like the clock signal, it
has to be debounced. Since the button is a switch to ground (GND), a pushed button shows as reading a LOW state. The (after debouncing) valid state of the button is stored in the semaphore rot_button. The variable is true, if a button push is detected.

Processing the rotary encoder in the main loop is fairly simple. Just the previously mentioned semaphores have to be monitored.

Detecting the button:

lcd.setCursor(14,0);
if (rot_button==true) { | // rotary encoder:
// button pushed
rot_button = false; | // reset this flag
// after detection
Serial1.print("Button->set (Channel ");
if (stepper == step_cha) {
Serial1.println("A)");
| }
else {
Serial1.println("B)");
| }
}

Drafted by Sven Petersen | Page 10 of 22 | Doc.-No.: 174-6-01-00

Or the direction of rotation:

if (rot_value != 0) {
if (rot_value < 0) {
num_steps = num_steps - 10; rot_value++;
}
else {
num_steps = num_steps + 10; rot_value--;
}
lcd.setCursor(7,1);
lcd.print( num_steps );
lcd.print( " " );
Serial1.print( "Steps: " ); Serial1.println( num_steps ); }
Here the number of steps (num_steps) is reduced by 10 on each “click” while rot_value is < 0
(direction = CCW) and increased by 10 while rot_value is > 0 (direction = CW).

RS-232
Other than the “regular” serial (via USB) interface, this RS-232 is addressed as Serial1 in the Arduino
IDE. The programming works like with the first serial interface. The recommended reading is https://www.arduino.cc/reference/en/language/functions/communication/serial/.

The initialization works with

Serial1.begin(9600);// the RS232 interface (RX, TX on pin 0 and 1) is
// Serial1.

This the 9600 bit/s (aka 9600 baud), 8N1 (8 data bits, No parity, 1 stop bit), a very common baud rate and data format.

Sending text via the serial interface is fairly simple:

Serial1.println( "Hello RS-232" ); // say hello

The RS-232 interface is also for receiving commands from a host. To collect this data and later process it (parsing the string = extracting the commands and parameters), some RAM space (a buffer) is allocated. For the parsing, the String functions are required

String recString = ""; // receive command buffer
[…]

recString.reserve(80);

A process, that is executed on every event on the Serial1 (RS-232) interface is

void serialEvent1() {
while (Serial1.available()) { | // bytes available on Serial1?
recByte = (char)Serial1.read(); | // read it
if (recByte == (char)10) { | // is it "new line character"?
recComplete = true; | // yes: the line is complete
}
else {

Drafted by Sven Petersen | Page 11 of 22 | Doc.-No.: 174-6-01-00
recString += recByte; | | // no: append character to input
string
}
}
}

As long as there is data available on the interface, it is checked, if the data byte (actually a character) is a “Line Feed” (= (char)10 ). The line feed denotes the end of a command string. If so, a semaphore (recComplete) is set true. If it is a different character, this will be appended to the buffer recString.

The parsing of the received string in the main loop looks like this:

if (recComplete) { | // a complete command line is received on RS-232
lcd.setCursor(0,1); | // position the cursor on the second line
lcd.print( recString ); | | // print the received string
lcd.print( " | " ); | // clear the line after that string
recString.toUpperCase(); | | // convert the line to upper case
| | // (it is not case sensitive)
syntaxError = false; | | // reset the Syntax Error flag
if (recString[0] == 'A') { | // is the first character an A?
stepper = step_cha; | // yes: select Stepper#1 (channel A)
}
else | if (recString[0] == 'B') { // is the first character a B?
stepper = step_chb; | // yes: select Stepper#2 (channel B)
}
else {
syntaxError = true; | // else, the syntax is not correct.
}
if (!syntaxError) { | // syntax still correct?
int pos = (int) recString.indexOf(","); // find the first comma ","
if (pos < 1) { | // if no comma is found
syntaxError = true; | // set the Syntax Error Flag
}
else { | // a comma is found:
recString.remove(0,pos+1); | // remove the beginning, the comma
// included
num_steps = (int) recString.toInt();// convert the string to
// integer -> num_steps
if (num_steps<0) { | // is it a negative number?
num_steps = -num_steps; | // yes: make it positive
st_direction = step_ccw; | // the direction is counterclockwise
}
else { | // no:
st_direction = step_cw; | // the direction is clockwise
}
digitalWrite( dir1, | st_direction | ); | // set the direction of both
digitalWrite( dir2, | st_direction | ); | // stepper motors
}
}
if (syntaxError) {
Serial1.println("? SYNTAX ERROR"); // report the syntax error }
else {
Serial1.print("Execute: Channel "); // report the execution switch (stepper) {
case step_cha: {

Drafted by Sven Petersen | Page 12 of 22 | Doc.-No.: 174-6-01-00
Serial1.print("A, "); | // Channel A
break;
}
case step_chb: {
Serial1.print("B, "); | // Channel B
break;
}
}
Serial1.print( num_steps ); | // and the number of steps
if (st_direction == step_cw) {
Serial1.println(" steps, CW"); | // and the direction
}
else {
Serial1.println(" steps, CCW");
}
}
recComplete = false; | // reset the semaphore
recString = ""; | // reset the recString (receive buffer)

The command line will let the selected stepper motor turn CW or CCW by the sent number of steps.

A proper command line looks like this:

<channel>, <number of steps>

While <channel> is A or B or a or b (it is not case sensitive) and a positive <number of steps> will turn the clockwise and a negative <number of steps> will turn counter clockwise.

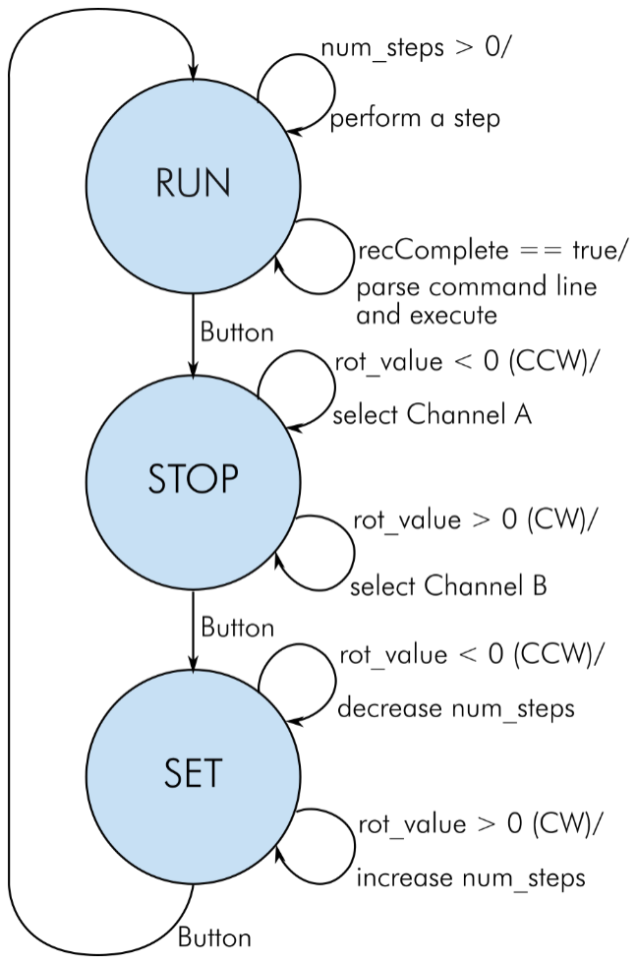
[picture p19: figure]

Drafted by Sven Petersen | Page 13 of 22 | Doc.-No.: 174-6-01-00

### State Machine

The main loop is designed as a (finite-)state machine. This is a very common structure for micro controller software, which is quite useful to know.

Depending on the state, the actions and reactions are different. This (desired) behavior can be depicted in a state diagram (Figure 3).

Figure 3: State diagram

The state machine has three states: RUN, STOP and SET. The states are represented by int values defined like this:

// state machine states
#define sm_stop // assigning a numbers to the state machine states #define sm_set 1

#define sm_run 2

The state RUN is entered first, it checks, if num_steps is greater 0, if so, it performs a step and decreases num_steps by one.

Also, it checks, if a command line (via RS-232) is complete (recComplete is true), if so, the command line is parsed and executed.

In case the push button of the rotary encoder is pressed, it enters the state STOP.

The state STOP watches the rotary encoder. If it is turned counterclockwise, Stepper channel A is selected, if it is clockwise, Stepper channel B is selected.

If the push button is pushed, the state SET becomes active.

Drafted by Sven Petersen | Page 14 of 22 | Doc.-No.: 174-6-01-00

While SET the number of steps to perform next and the direction is adjusted. If the rotary encoder is turned clockwise, the variable num_steps is increased by 10, while counterclockwise, num_steps is increased by 10. A negative number will select counterclockwise for both stepper motors. Pressing the push button will enter the state RUN.

The over-all structure of the state machine is a switch/case construction in the main loop.

switch (state_machine) {
case sm_stop : {
[…]

break;
}

case sm_set : {
[…]

break;
}
case sm_run : {
[…]

break;
}
}

## Connector Pinouts

### J1 - Power Connector

J1 is a 2.5mm/5.5mm barrel jack.

Pin | Signal
Inner | +12VDC
Outer | GND

### J2 – RS-232 Serial Interface

D-Sub, 9 pins, female

Pin | Signal | Note
1 | DCD | Feedback DCD – DTR - DSR
2 | RxD | Output
3 | TxD | Input
4 | DTR | Feedback DCD – DTR – DSR
5 | GND | Ground
6 | DSR | Feedback DCD – DTR – DSR
7 | RTS | Feedback RTS - CTS
8 | CTS | Feedback RTS – CTS
9 | RI | Not connected

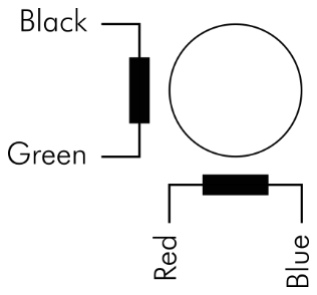
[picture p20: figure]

Drafted by Sven Petersen | Page 15 of 22 | Doc.-No.: 174-6-01-00

### J3 – Rotary Encoder

KF2510 series, 5pin (or Molex P/N 22272051) – vertical header with friction lock. Pinout for KY-040 rotary encoder module.

Pin | Signal | Note
1 GND
2 +5V
3 | Switch | Button
4 | Data | Actually, Channel A
5 | Clock | Actually, Channel B

The counterpart of J3 is a crimp housing (also KF2510 series, which is wide spread on Ebay, AliExpress and other online shops) and fitting crimp terminals. Alternatively, Molex P/N 22013047 and crimp terminal P/N 0850-0114 can be used.

### J4, J5 – Stepper Motor Outputs

KF2510 series, 4pin (or Molex P/N 22272041) – vertical header with friction lock or horizontal (90°) Molex P/N 22057048. J4 is Channel A/Stepper 1, J5 is Channel B/Stepper 2.

Pin | Signal | Note
1 | 1B | stepper motor blue cable
2 | 1A | stepper motor red cable
3 | 2A | stepper motor green cable
4 | 2B | stepper motor black cable

Figure 4: Windings of the stepper motor/cable colors

### J6 – Reserved I/O-Pins

The free GPIO-Pins of the Pro Micro are connected to a pin header (6 pins, 2.54mm pitch) which does not require to be placed. These pins might serve for connecting sensors/switches/actors

Pin | Signal | Note
1 GND
2 | D16 | GPIO D16, PCINT2
3 | A0 | Analog input/GPIO
4 | A1 | Analog input/GPIO
5 | A2 | Analog input/GPIO
6 | A3 | Analog input/GPIO

### J7 – I²C/Display Connector

KF2510 series, 4pin (or Molex P/N 22272041) – vertical header with friction lock. Pinout for LCD Displays (16x2) with I²C controller.

Drafted by Sven Petersen | Page 16 of 22 | Doc.-No.: 174-6-01-00
Pin | Signal | Note
1 | SCL | I²C clock
2 | SDA | I²C data
3 +5V
4 GND

The counterpart of J7 is a crimp housing (also KF2510 series, which is wide spread on Ebay, AliExpress and other online shops) and fitting crimp terminals. Alternatively, Molex P/N 22012041 and crimp terminal P/N 0850-0114 can be used.

### J8 – TX/RX Reserve Header

The TX and RX signals are routed to a pin header (3 pins, 2.54mm), which is not placed, in case it is desired to repurpose them or to watch the data exchange on the serial port/RS-232.

Pin | Signal | Note
1 GND
2 | TX | serial output, GPIO D1
3 | RX | serial input, GPIO D2

## Jumpers

There are two jumpers, JP1 and JP2. Both serve the setting of the step modes (full step, ½ step, ¼ step, 1/8 step and 1/16 step). JP1 determines the mode of stepper #1/channel A, JP2 does so for stepper#2/channel B).

MS1 / JPx 1-2 | MS2 / JPx 3-4 MS3 / JPx 5-6 Mode/micro step resolution
L/open | L/open | L/open | Full Step
H/set | L/open | L/open | Half Step
L/open | H/set | L/open | Quarter Step
H/set | H/set | L/open | Eighth Step
H/set | H/set | H/set | Sixteenth Step

The footprints of the jumpers allow fix solder bridges instead of a pin header and jumper.

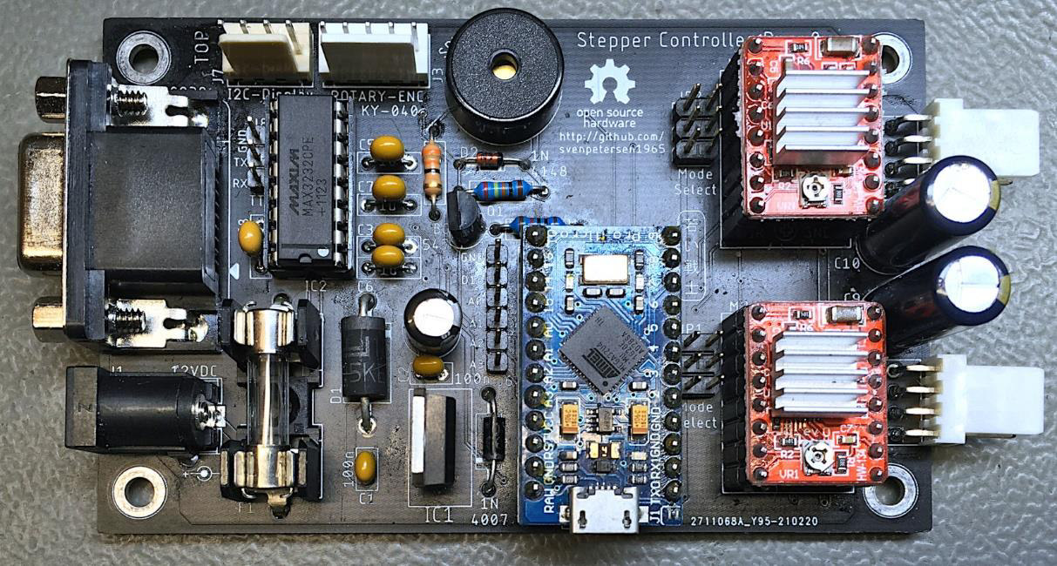
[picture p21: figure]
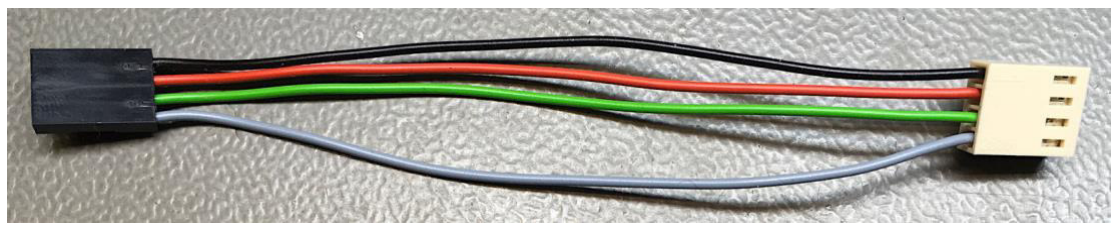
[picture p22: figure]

Drafted by Sven Petersen | Page 17 of 22 | Doc.-No.: 174-6-01-00

## Assembly

### The PCB

The PCB can be fully populated or some not requires parts can be omitted.

Figure 5: Fully populated PCB

Requirement | Components
Always populate | J1, F1, C1, C2, C4, D3, M1, M2, C9, J4
2 nd stepper controller | M3, C10, J5
Buzzer | R1, R1, R2, R3, D2, SPK1
Display | J7
Rotary Encode | J3
RS-232 | J2, IC2, C3, C5, C6, C7, C8
Micro steps required and jumpered | Channel A: JP1, Channel B: JP2. A fix setting of the jumpers can be accomplished with solder bridges
Do not place (until required) | J6, J8

### Cables

In case the 90° pin headers are used for the stepper motor connection (J4, J5), there are only two cables required:

### 1. the display cable 2. the rotary encoder cable

Figure 6: The display (I²C) cable

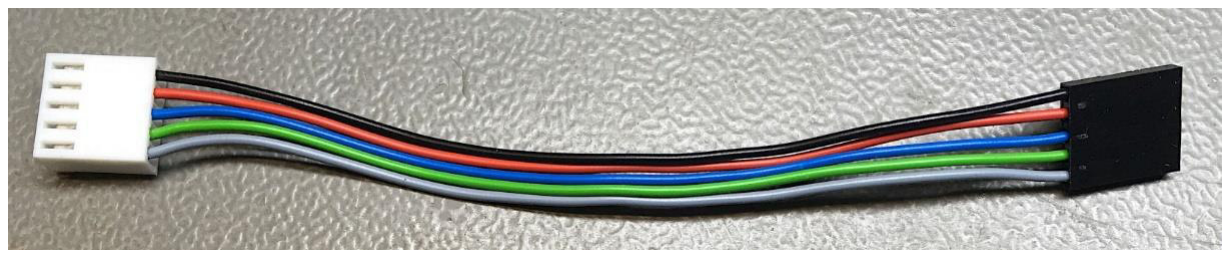
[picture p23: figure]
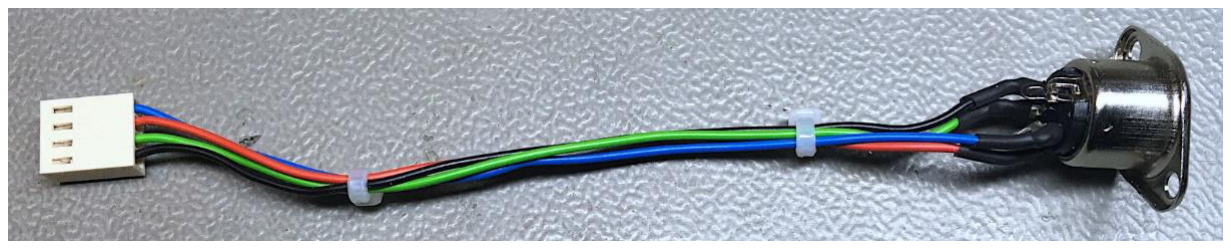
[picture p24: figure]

Drafted by Sven Petersen | Page 18 of 22 | Doc.-No.: 174-6-01-00

This display cable consists of the following components:

Pos. | Qty | Part
1 | 1 | DuPont crimp housing, 4 pins
2 | 4 | DuPont crimp terminals
3 | 14cm | Cable, 0.25mm²/AWG24, black
4 | 14cm | Cable, 0.25mm²/AWG24, red
5 | 14cm | Cable, 0.25mm²/AWG24, green
6 | 14cm | Cable, 0.25mm²/AWG24, grey
7 | 4 | KF2510 crimp terminals
8 | 1 | KF2510 crimp housing, 4 pins

The colors of the cables are a suggestion only.

Figure 7: Rotary encoder cable

This rotary encoder cable consists of the following components:

Pos. | Qty | Part
1 | 1 | DuPont crimp housing, 5 pins
2 | 5 | DuPont crimp terminals
3 | 14cm | Cable, 0.25mm²/AWG24, black
4 | 14cm | Cable, 0.25mm²/AWG24, red
5 | 14cm | Cable, 0.25mm²/AWG24, blue
6 | 14cm | Cable, 0.25mm²/AWG24, green
7 | 14cm | Cable, 0.25mm²/AWG24, grey
8 | 5 | KF2510 crimp terminals
9 | 1 | KF2510 crimp housing, 5 pins

Optionally, a DIN connector can be used for the stepper motor connections.

Figure 8: Stepper cable (internal, optional)

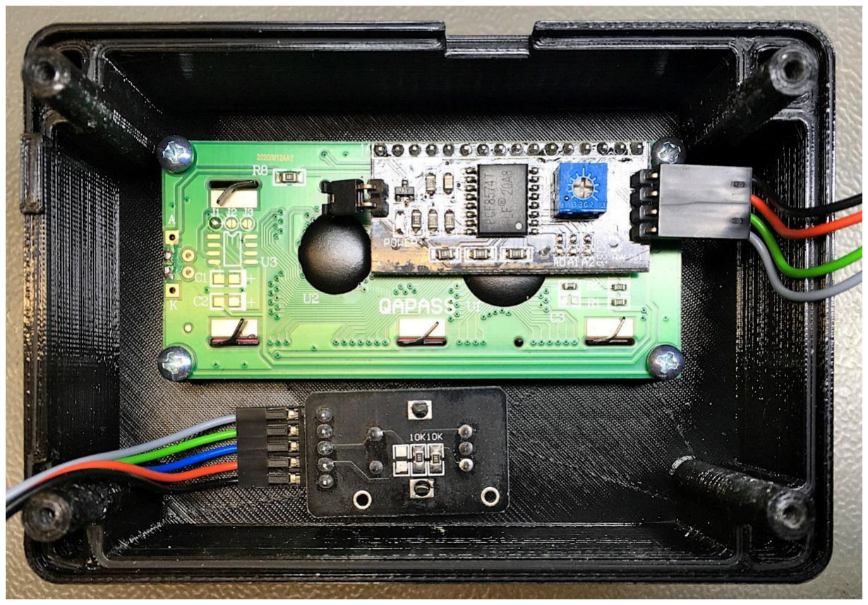
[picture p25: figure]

Drafted by Sven Petersen | Page 19 of 22 | Doc.-No.: 174-6-01-00
Pos. | Qty | Part
1 | 1 | DIN Jack, 5 pins (e.g. Reichelt MAB 5S)
2 | 14cm | Cable, 0.25mm²/AWG24, black
3 | 14cm | Cable, 0.25mm²/AWG24, green
4 | 14cm | Cable, 0.25mm²/AWG24, red
5 | 14cm | Cable, 0.25mm²/AWG24, blue
6 | 5 | KF2510 crimp terminals
7 | 1 | KF2510 crimp housing, 5 pins
8 | 6cm | Shrinkable sleeve (2.4/1.2)

### 3D Printed Case

It is recommended to use the 3D printed case for this project. It consists of a top and a bottom shell and is constructed in Fusion 360. The STL files for 3D printing are provided as well as the Fusion 360 project.

The display is attached with 4 screws (C2.9x6.5 DIN 7981 recommended). The rotary encoder is attached with the nut included in it. The cables should be connected prior to mounting those components.

Figure 9: Top shell with mounted LCD display and rotary encoder KY-040

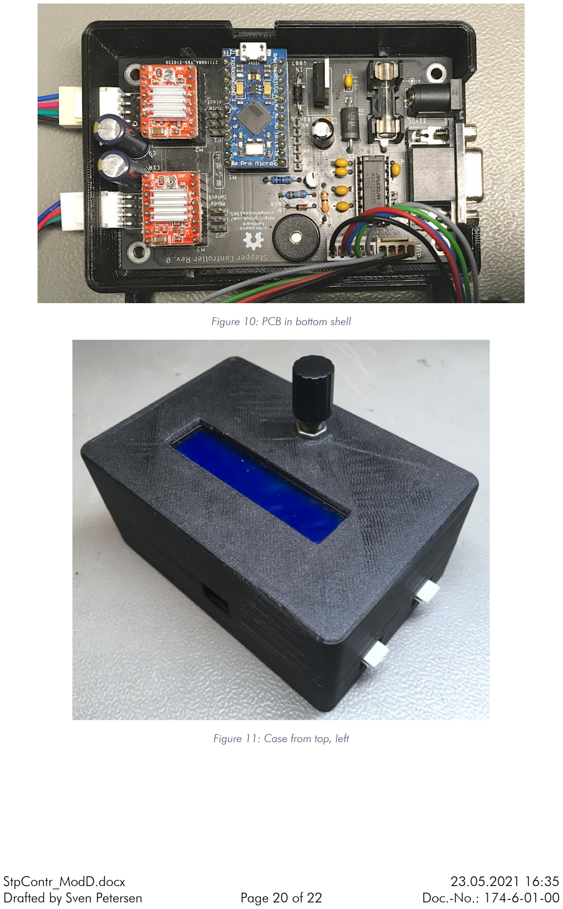
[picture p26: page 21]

Drafted by Sven Petersen | Page 20 of 22 | Doc.-No.: 174-6-01-00

Figure 10: PCB in bottom shell

Figure 11: Case from top, left

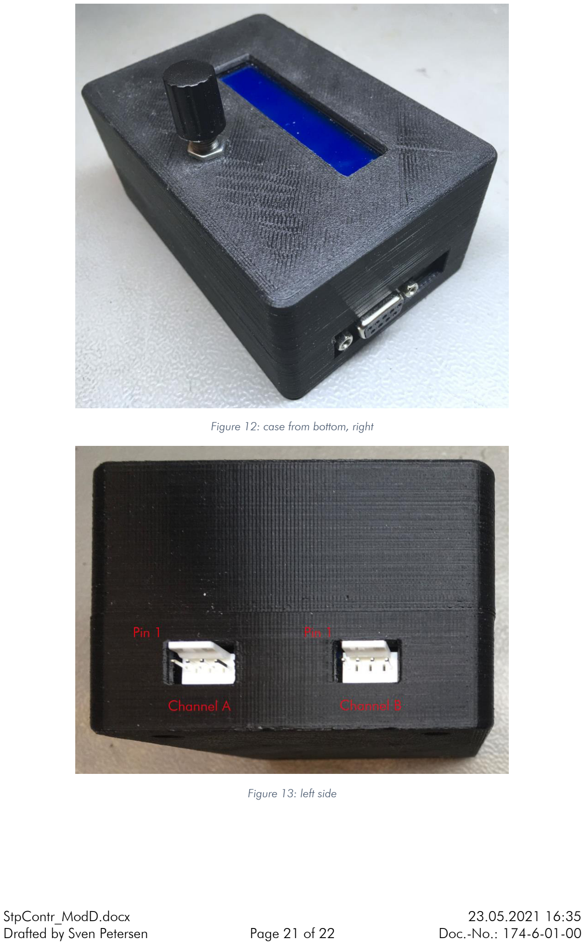
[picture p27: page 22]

Drafted by Sven Petersen | Page 21 of 22 | Doc.-No.: 174-6-01-00

Figure 12: case from bottom, right

Figure 13: left side


Drafted by Sven Petersen | Page 22 of 22 | Doc.-No.: 174-6-01-00

Figure 14: right side

There are different versions of the top and bottom shell provided. The top shell can have a mounting space for a DIN connector (that could serve as a stepper motor connector), the bottom shell can have the cut outs for the 90° stepper motor connector as shown in Figure 10.

For closing the case, with 4 screws (C2.9x13 DIN 7981 recommended) are required.

## Revision History

### Rev. 0

- Fully functional prototype










StpContr_FunD.docx | | 23.05.2021 16:36
Drafted by Sven Petersen | Page 1 of 1 | Doc.-No.: 174-6-02-00

### Stepper Motor Controller Rev. 0

### Functional Description

J1 is the power supply connector. F1 is the 5x20mm fuse, which might require to be adjusted to the application/stepper motors. D1 is a TVS diode for transient (0voltage spike) suppression. It is calculated for a 12V supply voltage. In case a different supply voltage is desired, a different TVS diode has to be selected.

IC1 is shown as a Traco TRS2-2450 DC/DC converter. Since this is pin compatible to the standard linear regulators, a 7805 can be populated instead of the DC/DC converter, which might be required for higher supply voltages (e.G. 24V for 24V stepper motors).

D3 is a protection when switching off the Stepper motor controller. It helps that the output voltage of IC1 is not much higher than the input voltage (due to charged capacitors).

M1 is a Pro Micro, a popular Atmel Atmega32U4 based micro processor module, which is compatible to the Arduino Leonardo. To send the program/script to the Pro Micro, the USB-B micro connector has to be connected to the PC, the Arduino IDE software is running, the Arduino Leonardo is selected and the proper COM-Port.

IC2 is the level translator for RS-232 (the logic levels of RS-232 are about +/-10V with the MAX232. C3, C5, C6 and C7 are part of the charge pump for generating the required voltages for the IC2. J2 is the RS-232 jack. CTS and RTS are connected as well as DTR, DSR and DCD.

J8 can be used to repurpose the RX and TX pins or for spying the serial traffic at TTL level.

J6 is a pin header for the unused I/O pins of M1. It usually does not require to be populated.

The circuit around Q1 serves as a buzzer amplifier/protection circuit. Actually, an IO-Pin of M1 could drive the buzzer, but the buzzer can act as a high voltage spike generator on a mechanical impact. Thus, the circuit. R1 is the base resistor of Q1, R2 is for current limiting, D2 is kind of a free-wheeling diode, that helps to prevent reverse voltages.

M2 and M3 are the Allegro A4988 based stepper drivers. M2 is for Channel A/Stepper 1 and M3 for Channel B/Stepper 2. C9 and C10 are the buffer capacitors for VMOT, the +12V supply voltage for the stepper motors. JP1 and JP2 configure the micro step mode. All jumpers
open mean “full step”. An open jumper is interpreted as a LOW signale by the A4988.

There is one common Enable Signal ( STP_EN ) for both stepper motors. In case it is LOW, the stepper motors are active and the axis cannot be moved manually. It performs steps in this mode. In case STP_EN is HIGH, no current flows through the stepper windings and the axis can be moved manually (at least, if the stepper does not have a gear).

J7 is a connector for the I²C-Bus. Usually, a display is connected. Since the I²C is a bus, additional I²C devices can be connected.

J3 is a connector for the rotary encoder. A KY-040 module, which is pretty wide spread and unexpensive can be connected here.


StpContr_Test.docx | | 23.05.2021 16:36
Drafted by Sven Petersen | Page 1 of 4 | Doc.-No.: 174-6-03-00

### Stepper Motor Controller Rev. 0

### Testing

## Test Setup

### Hardware

A fully populated Stepper Motor Controller Rev. 0 with a 16x2 I²C LCD-display was tested with three different stepper motors:

1. 17HS13-0404S (NEMA17, 12V, 0.4A/phase, 1.8° steps)
2. 17HS8-1004S (NEMA17, 12V, 1A/phase, 1.8° steps)
3. 17HS13-0404S-PG5 ((NEMA17, 12V, 0.4A/phase, 1.8° steps, 1:5.182 gear)

The voltage supply is a Goobay SE120P3000EU (12V/3A output on a 2.5mm/5.5mm barrel connector).

A USB-RS-232-Adapter was used for testing then RS-232 interface.
The software “stepper_framework.ino” was uploaded to the Pro Micro via the USB interface.

Figure 1: Test Setup

### YAT – Terminal Program

To communicate with the Stepper Motor Controller via RS-232, a terminal program is required. The serial monitor of the Arduino IDE only works on the COM-Port, that is selected for sending the sketch.
A recommended one is YAT (“Yet, Another Terminal”).

https://sourceforge.net/projects/y-a-terminal/files/latest/download


StpContr_Test.docx | | 23.05.2021 16:36
Drafted by Sven Petersen | Page 2 of 4 | Doc.-No.: 174-6-03-00

## Test Execution

### Software upload

The software “stepper_framework.ino” was uploaded with the Arduino IDE successfully.

### Power

After connection the +12V-PSU the Stepper Controller powered up properly. The +5V from the linear voltage regulator were measured as +5.03V at the stepper driver A4988. The +12V (12.3V without load) from the PSU were measured as +12.14V at the stepper driver, too.

Figure 2: Thermal measurement on linear regulator IC1
The supply current was measured while in the “STOP” state (no current through the stepper motor
windings). It is about 93.5mA. When in “RUN” state, a supply current of 850mA was observed. This does not change much while a stepper motor is running and mostly depends on the stepper motors used and the current adjustment of the stepper driver.

When powered from +12V, the linear regulator settles at about 57°C, which is non critical.

Time | Temperature
Start | 21.6°C
Start + 75 minutes | 56.9°C

The thermal resistance junction-case (RthJC) is 5K/W according to the data sheet. The dissipated power is

# PD = (Vin − Vout) ∙ I = (12V − 5V) ∙ 93.5mA = 0.655W


StpContr_Test.docx | | 23.05.2021 16:36
Drafted by Sven Petersen | Page 3 of 4 | Doc.-No.: 174-6-03-00

Hence, the estimated junction temperature is

# θJunction = θCase + RtℎJC ∙ PD = 56.9°C + 5

°C
W
- 0.655W ≅ 60.2°C

This is far below the absolute maximum rating of 150°C.

The measurements were executed with a EEVBlog 121GW multimeter. The thermo couple was fixed to the backside of the 78S05/IC1 (refer to Figure 2). The case was closed for the thermal measurement.

### Piezo Buzzer

The piezo buzzer beeps after switching on the power. It can be heard well even while the case is closed.

### LCD Display

The LCD display initialized properly and the text appeared as desired. The contrast had to be adjusted slightly (potentiometer on the LDC-display).

### Rotary Encoder

The push button and both directions were detected properly with the installed software.

### Stepper Driver

Both stepper motors executed the full steps set with the rotary encoder. Both directions work. Further, the half, quarter, 1/8 and 1/16 micro-steps were configured with the jumpers. The micro-steps were not carried out evenly, so an adjustment of the stepper current (potentiometer on the A4988 modules) was required. After setting the current limit properly, the steps were carried out evenly. The setting
was adjusted “by ear”.

All three stepper motors were tested.

### RS-232 Interface

The RS-232 serial interface was tested with YAT (set to 9600baud, 8N1).

Figure 3: Terminal Program YAT communicating with the Stepper Motor Controller

StpContr_Test.docx | | 23.05.2021 16:36
Drafted by Sven Petersen | Page 4 of 4 | Doc.-No.: 174-6-03-00

Both, the send and receive direction work properly. The messages from the stepper controller were displayed correctly in YAT and the sent command were recognized by the stepper controller and executed.

## Conclusion

The Stepper Motor Controller is working properly. The DC/DC-converter has not been tested.

Pos. Qty Value Footprint Ref.-No. Comment

1 1 174-2-01-00 2 Layer PCB Rev. 0 2 layer, Cu 35µ, HASL, 99.0mm x 62.0mm, 1.6mm FR4

2 2 KF2510 (vertical, 4pin) 6410-4P J4, J5 or Molex 22-27-2041 (vertical, Reichelt MOLEX 22272041

or tme.eu:MX-6410-04A) or Molex P/N 22057048

(horizontal/90°, Reichelt: MOLEX 22057048 or tme.eu: MX-

7395-04B)

3 1 KF2510 (vertical, 4pin) 6410-4P J7 or Molex 22-27-2041 (always vertical, Reichelt MOLEX

22272041 or tme.eu:MX-6410-04A)

4 3 KF2510 crimp housing, 4

pins

(J4), (J5), (J6) or Molex 22013047 (Reichelt: MOLEX 22013047, tme.eu:

MX-22-01-3047)

5 12 KF2510 crimp terminals (J4), (J5), (J6) or Molex 08500114 (Reichelt: MOLEX 8500114) or Molex

08-70-0049 (tme.eu: MX-08-70-0049)

6 1 KF2510 (vertical, 5pin) 6410-5P J3 or Molex 22-27-2051

7 1 KF2510 crimp housing, 4

pins

(J3) or Molex 22013057

8 5 KF2510 crimp terminals (J3) or Molex 08500114 (Reichelt: MOLEX 8500114) or Molex

08-70-0049 (tme.eu: MX-08-70-0049)

9 1 MAX232CPE DIL-16 IC2 Maxim or Renesas HIN232CPZ (Reichelt: MAX 232 DIP,

tme.eu: HIN232CPZ)

10 1 pin header, 3 pin, 2.54mm

pitch

1X03 J8 DNP

11 1 pin header, 6 pin, 2.54mm

pitch

1X06 J6 DNP

12 1 0031.8211 318211 F1 Schurter fuse holder (Reichelt: PL OGN-25, tme.eu:

0031.8211)

13 1 5x20mm, 3.15AT (F1) This fuse depends on the power supply and the application
14 1 1,5KE12A DO-201 D1 TVS-Diode, unidirektional, (Reichelt: 1,5KE 12A, tme.eu:

1.5KE12A-LF)

15 2 100n C-2,5 C1, C2 ceramic capacitor, 2.5mm pitch

16 1 10k R-10 R1 metal film resistor, 0.5W (or more), 5% or better

## Stepper Motor Controller Rev. 0

## Bill of Material Rev. 0.0

StpContr_BOM_v0_0.xlsx

Drafted by Sven Petersen Page 1 of 3

21.05.2021 18:32
Doc.No.: 174-5-01-00.0

Pos. Qty Value Footprint Ref.-No. Comment

## Stepper Motor Controller Rev. 0

## Bill of Material Rev. 0.0

17 1 1N4007 DO-41 D3 diode

18 1 1N4148 DO-35 D2 diode

19 5 1u C-5 C3, C5, C6, C7, C8 ceramic capacitor, 5mm pitch (e.g. Reichelt Z5U-5 1,0µ)

20 1 27k R-10 R3 metal film resistor, 0.5W (or more), 5% or better

21 1 33R R-10 R2 metal film resistor, 0.5W (or more), 5% or better

### 22 2 470u/25V C08/3,5 C9, C10 e-cap, ∅8mm, pitch 3.5mm, 105°C, e.g. Reichelt RAD FC

470/25

### 23 1 47u/50V C07/2,5 C4 e-cap, ∅7mm, pitch 2.5mm, 105°C, e.g. Reichelt RAD FC

47/50

24 1 BC547B TO92 Q1 universal NPN Transistor

25 2 COMBI-3X2P COMBI-3X2 JP1, JP2 see document 174-6-01-**. Reichelt MPE 087-2-006

26 1 DB09F_90° DS09F-H J2 D-Sub, 9pin, female, 90°, (Reichelt

27 1 FCR681465P FCR681465P J1 Cliff barrel connector (2.5mm/5.5mm), Reichelt: CLIFF

FCR681465P, tme.eu: FCR681465P

28 2 A4988 H4988 M2, M3 A4988 stepper driver module (AliExpress or Ebay etc.)

29 4 1x8 socket strip, 2.54mm (M2), (M3) e.g. MPE 115-1-008 (Reichelt: MPE 115-1-008, tme.eu:

ZL307-1X8)

30 1 PRO_MICRO PRO_MICRO M1 16MHz, 5V, Micro Controller module (Arduino compatible)
from AliExpress, Ebay etc. (ATTN: there are 8MHz, 3.3V

versions, too, which are not suitable

31 2 1x12 socket strip, 2.54mm (M1) e.g. MPE 115-1-012 (Reichelt: MPE 115-1-012, tme.eu:

ZL262-12SG)

### 32 1 RMP-14P/HT RMP-14P/HT SPK1 piezzo buzzer, ∅14mm, pitch 7.6mm, EKULIT (Reichelt

SUMMER EPM 121): alternative tme.eu LD-BZPN-1002 (on

cable)

33 1 7805 or TSR2-2450 TSR2 IC1 standard linear regulator or Traco DC/DC converter for

higher supply voltages

34 1 LCD Display I²C, 16x2 (J7) "standard" product from Ebay or AliExpress.

35 1 dupont crimp housing, 4

pins

For the I²C Display cable

StpContr_BOM_v0_0.xlsx

Drafted by Sven Petersen Page 2 of 3

21.05.2021 18:32
Doc.No.: 174-5-01-00.0

Pos. Qty Value Footprint Ref.-No. Comment

## Stepper Motor Controller Rev. 0

## Bill of Material Rev. 0.0

36 4 Dupont crimp terminals For the I²C Display cable

37 14cm cable, AWG24, black For the I²C Display cable, suggested color
38 14cm cable, AWG24, red For the I²C Display cable, suggested color
39 14cm cable, AWG24, green For the I²C Display cable, suggested color

40 14cm cable, AWG24, grey For the I²C Display cable, suggested color

41 1 KY-040 Rotary encoder, "standard" product from Ebay or AliExpress.

42 1 dupont crimp housing, 4

pins

for the rotary encoder

43 4 Dupont crimp terminals for the rotary encoder

44 14cm cable, AWG24, black for the rotary encoder, suggested color
45 14cm cable, AWG24, red for the rotary encoder, suggested color
46 14cm cable, AWG24, green for the rotary encoder, suggested color

47 14cm cable, AWG24, grey for the rotary encoder, suggested color
48 14cm cable, AWG24, blue for the rotary encoder, suggested color

StpContr_BOM_v0_0.xlsx

Drafted by Sven Petersen Page 3 of 3

21.05.2021 18:32
Doc.No.: 174-5-01-00.0

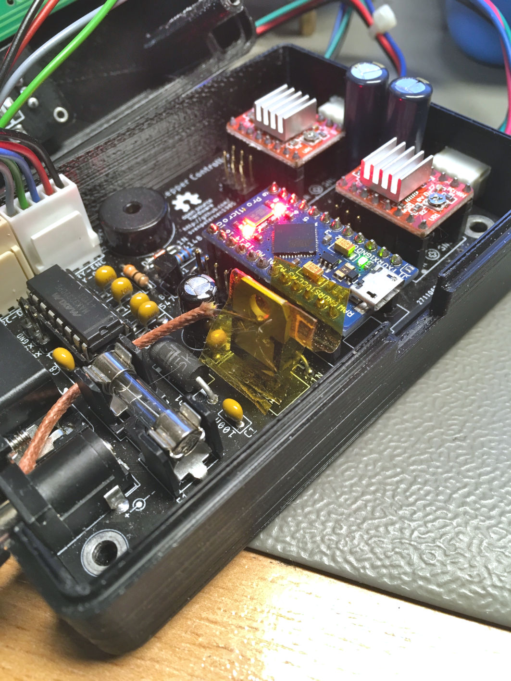
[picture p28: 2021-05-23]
Rev. 0/pictures/8488_-_IC1_thermal.JPG

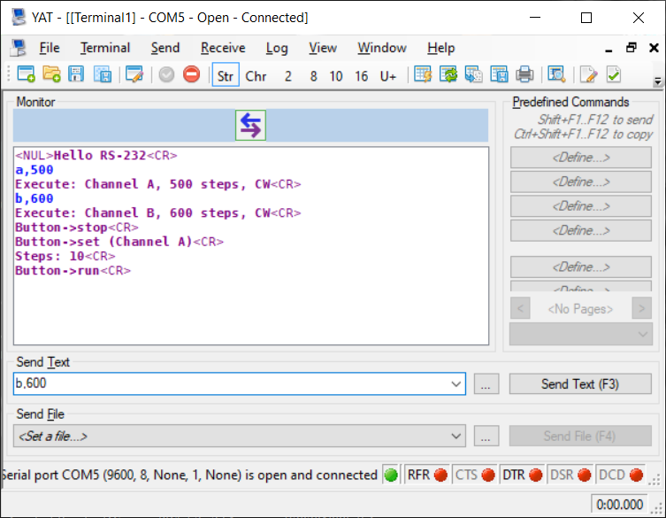
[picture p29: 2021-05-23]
Rev. 0/pictures/YAT.png

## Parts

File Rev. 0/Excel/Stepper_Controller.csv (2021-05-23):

Qty | Value | Device | Package | Parts | Description
3 |  | 6410-4P | 6410-4P | J4, J5, J7 | 6410/22-27-2041
1 |  | 6410-5P | 6410-5P | J3 | 6410/22-27-2051
4 |  | BOHR3,5 | BOHR3,5 | DRL1, DRL2, DRL3, DRL4
1 |  | MAX-232 | DIL-16 | IC2
1 |  | PINHD-1X3 | 1X03 | J8
1 |  | PINHD-1X6 | 1X06 | J6
1 | 0031.8211 | 0031.8211 | 0031.8211 | F1
1 | 1,5KE12A | 1,5KE12A | DO-201 | D1
2 | 100n | CAP01 | C-2,5 | C1, C2
1 | 10k | RES04 | R-10 | R1
1 | 1N4007 | 1N4007 | DO-41 | D3
1 | 1N4148 | 1N4148 | DO-35 | D2
5 | 1u | CAP02 | C-5 | C3, C5, C6, C7, C8
1 | 27k | RES04 | R-10 | R3
1 | 33R | RES04 | R-10 | R2
2 | 470u/25V | C08/3,5 | C08/3,5 | C9, C10
1 | 47u/50V | C07/2,5 | C07/2,5 | C4
1 | BC547B | BC547B | TO92 | Q1 | NPN Transistor
2 | COMBI-3X2P | COMBI-3X2P | COMBI-3X2 | JP1, JP2
1 | DB09F_90° | DS09F-H-CL | DS09F-H | J2
1 | FCR681465P | FCR681465P | FCR681465P | J1
2 | H4988 | H4988 | H4988 | M2, M3
1 | OPEN_SOURCE_HW | OPEN_SOURCE_HW | OPENHW | U$2
1 | PRO_MICRO | PRO_MICRO | PRO_MICRO | M1
1 | RMP-14P/HT | RMP-14P/HT | RMP-14P/HT | SPK1
1 | TSR2-2450 | TSR2 | TSR2 | IC1

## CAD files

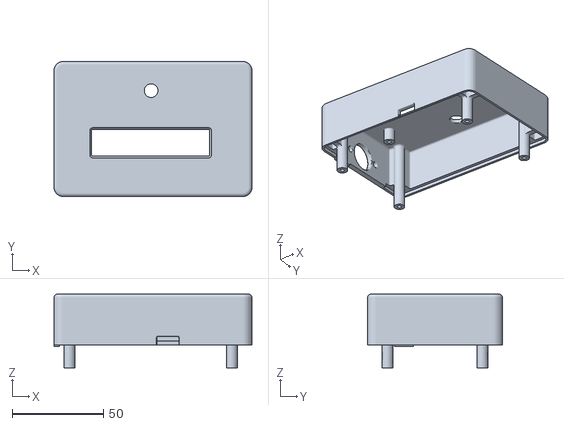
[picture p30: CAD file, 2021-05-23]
Case/stl/Stepper_controller_top_shell_DIN.stl
108.5 x 74.0 x 40.5

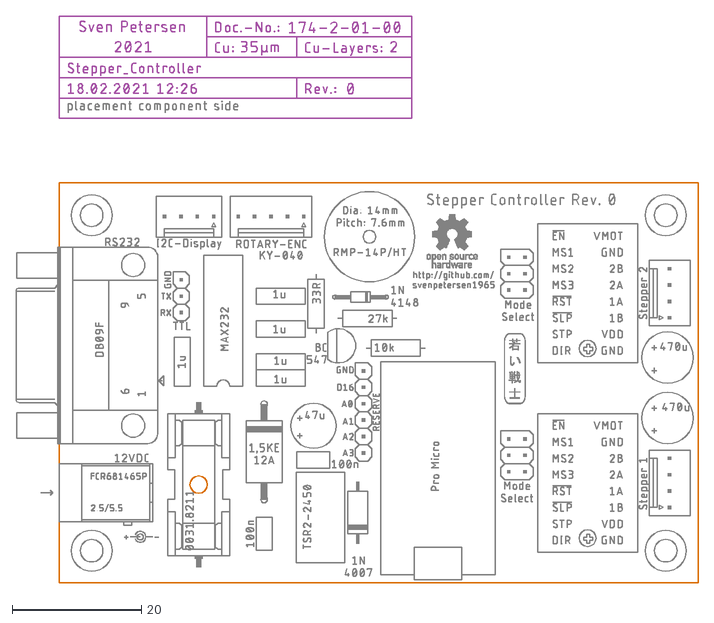
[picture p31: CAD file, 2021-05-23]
Rev. 0/dxf/Stepper_Controller.dxf
105.7 x 87.9

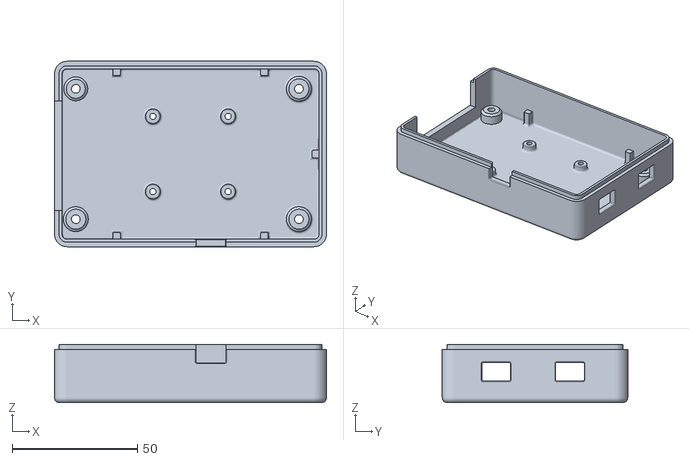
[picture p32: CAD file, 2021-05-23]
Case/stl/Stepper_controller_bottom_shell_stpcutout.stl
108.5 x 74.0 x 23.3

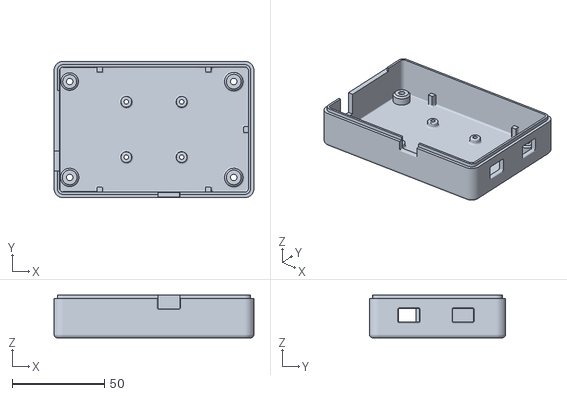
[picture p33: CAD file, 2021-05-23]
Case/stl/Stepper_controller_bottom_shell_stpcutout_noSer.stl
108.5 x 74.0 x 23.3

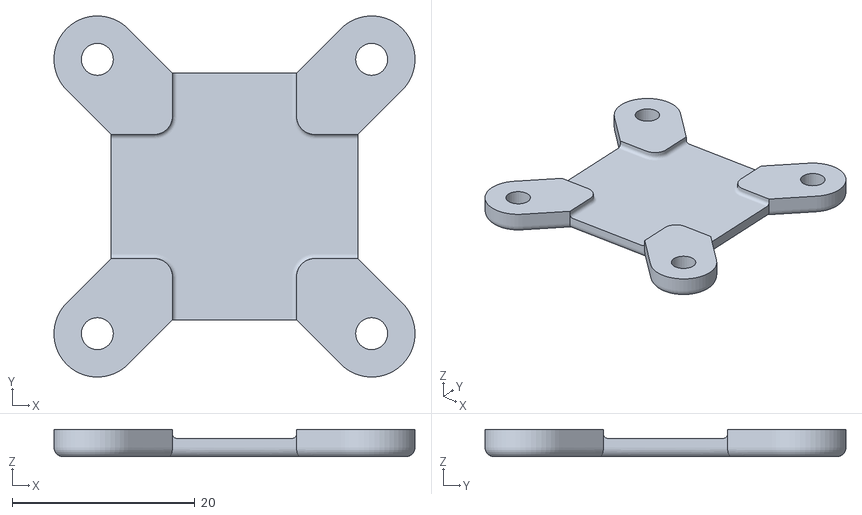
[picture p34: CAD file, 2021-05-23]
Case/stl/Stepper_controller_holder.stl
39.5 x 39.5 x 3.00

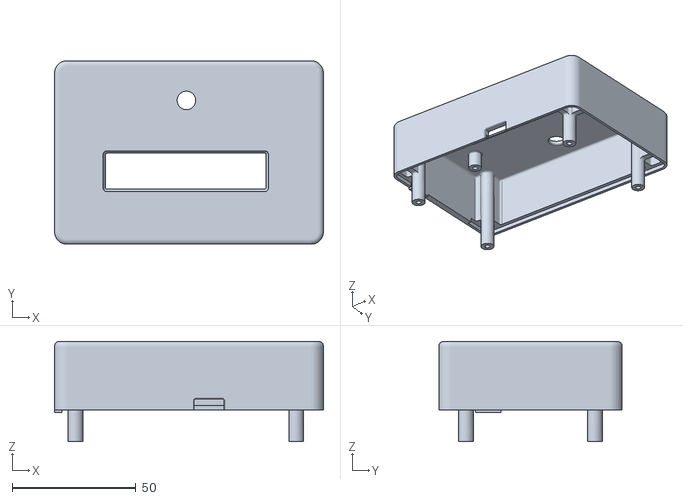
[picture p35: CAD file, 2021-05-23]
Case/stl/Stepper_controller_top_shell_noDIN.stl
108.5 x 74.0 x 40.5

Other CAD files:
Case/stl/Stepper_controller_bottom_shell_noStpCoutout.stl
Case/stl/Stepper_controller_bottom_shell_noSer.stl
Case/fusion360/stepper_controller_case v17.f3z

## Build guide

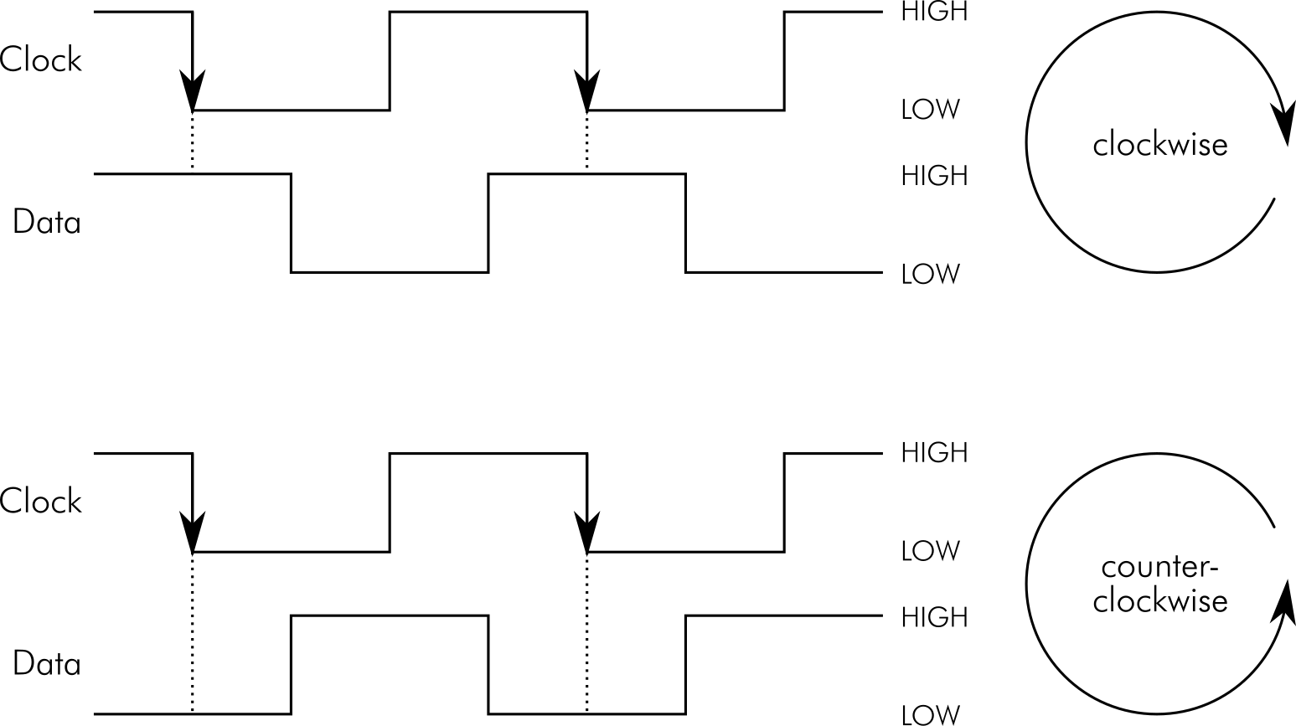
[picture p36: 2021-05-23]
Rev. 0/pictures/rotary_encoder_operation.png

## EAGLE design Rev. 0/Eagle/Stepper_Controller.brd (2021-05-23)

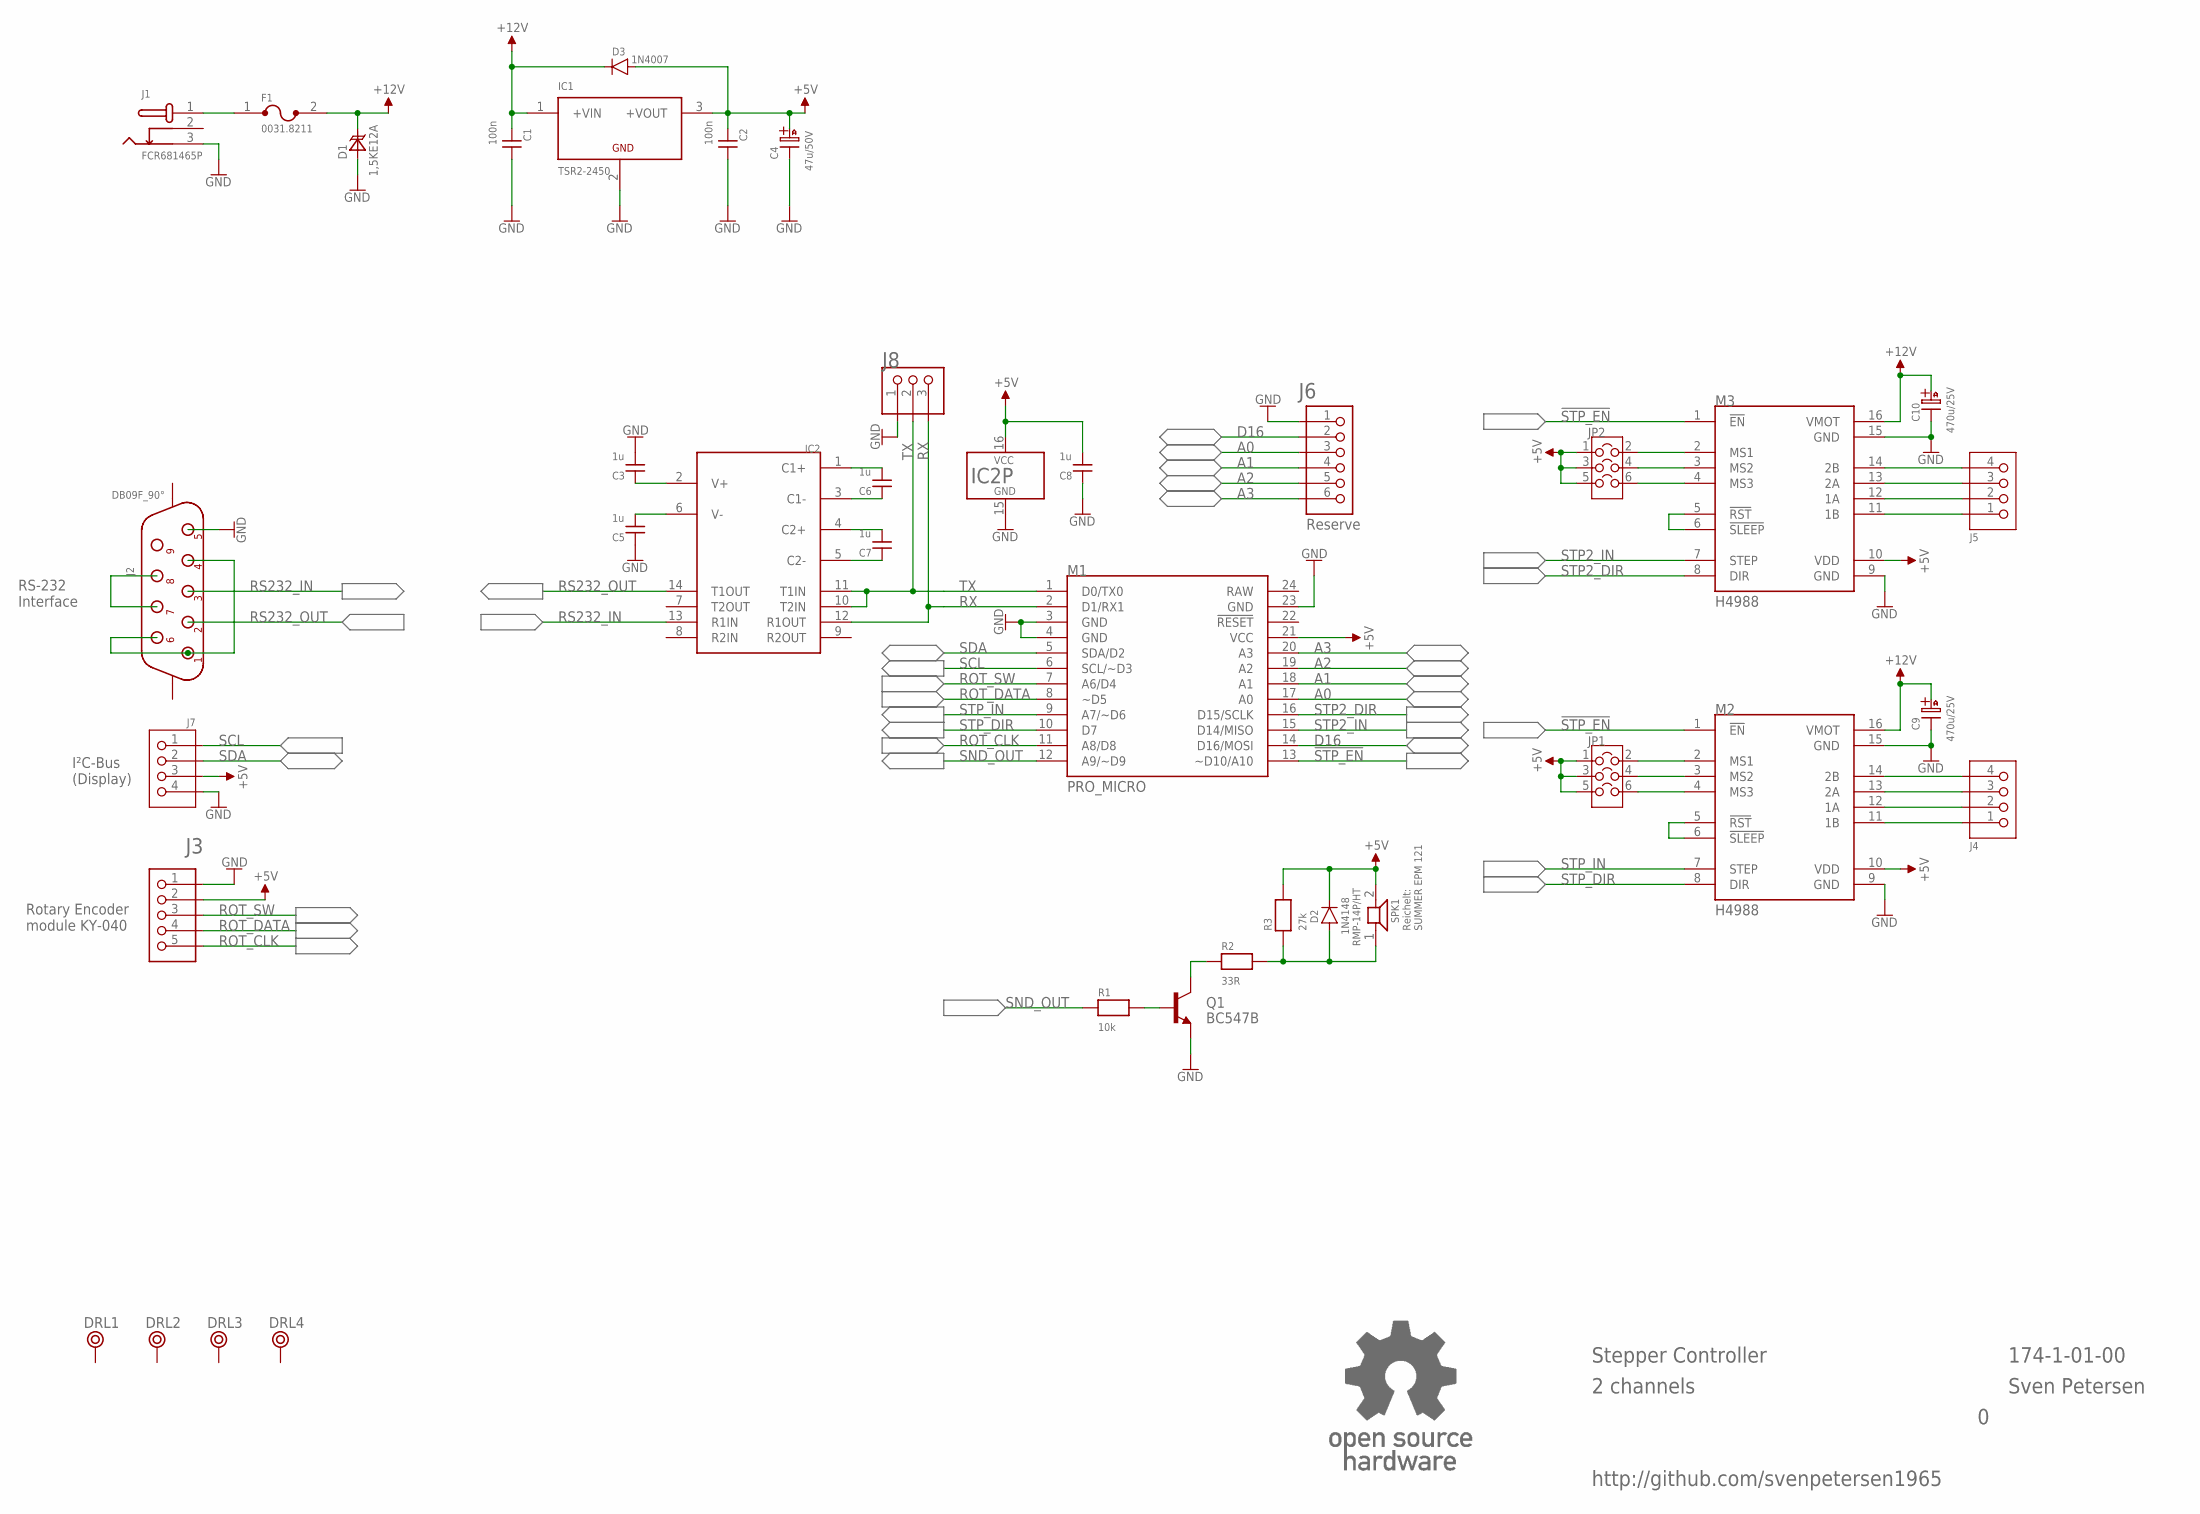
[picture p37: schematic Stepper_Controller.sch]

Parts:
C1, C2: 100n; C-2,5
C3, C5, C6, C7, C8: 1u; C-5
C4: 47u/50V; C07/2,5
C9, C10: 470u/25V; C08/3,5
D1: 1,5KE12A; DO-201
D2: 1N4148; DO-35
D3: 1N4007; DO-41
DRL1, DRL2, DRL3, DRL4: BOHR3,5
F1: 0031.8211
IC1: TSR2-2450; TSR2
IC2: MAX-232; DIL-16
J1: FCR681465P
J2: DB09F_90°; DS09F-H
J3: 6410-5P
J4, J5, J7: 6410-4P
J6: PINHD-1X6; 1X06
J8: PINHD-1X3; 1X03
JP1, JP2: COMBI-3X2P; COMBI-3X2
M1: PRO_MICRO
M2, M3: H4988
Q1: BC547B; TO92
R1: 10k; R-10
R2: 33R; R-10
R3: 27k; R-10
SPK1: RMP-14P/HT
U$2: OPEN_SOURCE_HW; OPENHW

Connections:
!STP_EN: M1.13 (~D10/A10), M2.1 (!EN), M3.1 (!EN)
+5V: C2.1, C4.A (+), C8.2, D2.K, D3.A, IC1.3 (+VOUT), IC2.16 (VCC), J3.2, J7.3, JP1.1, JP1.3, JP1.5, JP2.1, JP2.3, JP2.5, M1.21 (VCC), M2.10 (VDD), M3.10 (VDD), R3.2, SPK1.2
+12V: C1.1, C9.+, C10.+, D1.K, D3.K, F1.2, IC1.1 (+VIN), M2.16 (VMOT), M3.16 (VMOT)
A0: J6.3, M1.17 (A0)
A1: J6.4, M1.18 (A1)
A2: J6.5, M1.19 (A2)
A3: J6.6, M1.20 (A3)
D16: J6.2, M1.14 (D16/MOSI)
GND: C1.2, C2.2, C3.2, C4.K (-), C5.1, C8.1, C9.-, C10.-, D1.A, IC1.2 (GND), IC2.15 (GND), J1.3, J2.5, J3.1, J6.1, J7.4, J8.1, M1.3 (GND), M1.4 (GND), M1.23 (GND), M2.9 (GND), M2.15 (GND), M3.9 (GND), M3.15 (GND), Q1.1 (E)
unnamed: F1.1, J1.1
unnamed: Q1.3 (C), R2.1
unnamed: Q1.2 (B), R1.2
unnamed: J2.1, J2.4, J2.6
unnamed: J2.7, J2.8
unnamed: C7.2, IC2.4 (C2+)
unnamed: C7.1, IC2.5 (C2-)
unnamed: C6.1, IC2.3 (C1-)
unnamed: C6.2, IC2.1 (C1+)
unnamed: D2.A, R2.2, R3.1, SPK1.1
unnamed: C3.1, IC2.2 (V+)
unnamed: C5.2, IC2.6 (V-)
unnamed: M2.5 (!RST), M2.6 (!SLEEP)
unnamed: M3.5 (!RST), M3.6 (!SLEEP)
unnamed: JP2.2, M3.2 (MS1)
unnamed: JP2.4, M3.3 (MS2)
unnamed: JP2.6, M3.4 (MS3)
unnamed: JP1.2, M2.2 (MS1)
unnamed: JP1.4, M2.3 (MS2)
unnamed: JP1.6, M2.4 (MS3)
unnamed: J4.1, M2.11 (1B)
unnamed: J4.2, M2.12 (1A)
unnamed: J4.3, M2.13 (2A)
unnamed: J4.4, M2.14 (2B)
unnamed: J5.1, M3.11 (1B)
unnamed: J5.2, M3.12 (1A)
unnamed: J5.3, M3.13 (2A)
unnamed: J5.4, M3.14 (2B)
RAW: M1.24 (RAW)
ROT_CLK: J3.5, M1.11 (A8/D8)
ROT_DATA: J3.4, M1.8 (~D5)
ROT_SW: J3.3, M1.7 (A6/D4)
RS232_IN: IC2.13 (R1IN), J2.3
RS232_OUT: IC2.14 (T1OUT), J2.2
RX: IC2.12 (R1OUT), J8.3, M1.2 (D1/RX1)
SCL: J7.1, M1.6 (SCL/~D3)
SDA: J7.2, M1.5 (SDA/D2)
SND_OUT: M1.12 (A9/~D9), R1.1
STP2_DIR: M1.16 (D15/SCLK), M3.8 (DIR)
STP2_IN: M1.15 (D14/MISO), M3.7 (STEP)
STP_DIR: M1.10 (D7), M2.8 (DIR)
STP_IN: M1.9 (A7/~D6), M2.7 (STEP)
TX: IC2.10 (T2IN), IC2.11 (T1IN), J8.2, M1.1 (D0/TX0)

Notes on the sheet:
I²C-Bus (Display)
Reichelt: SUMMER EPM 121
RS-232 Interface
Rotary Encoder module KY-040
Reserve
Stepper Controller
2 channels
174-1-01-00
Sven Petersen
http://github.com/svenpetersen1965

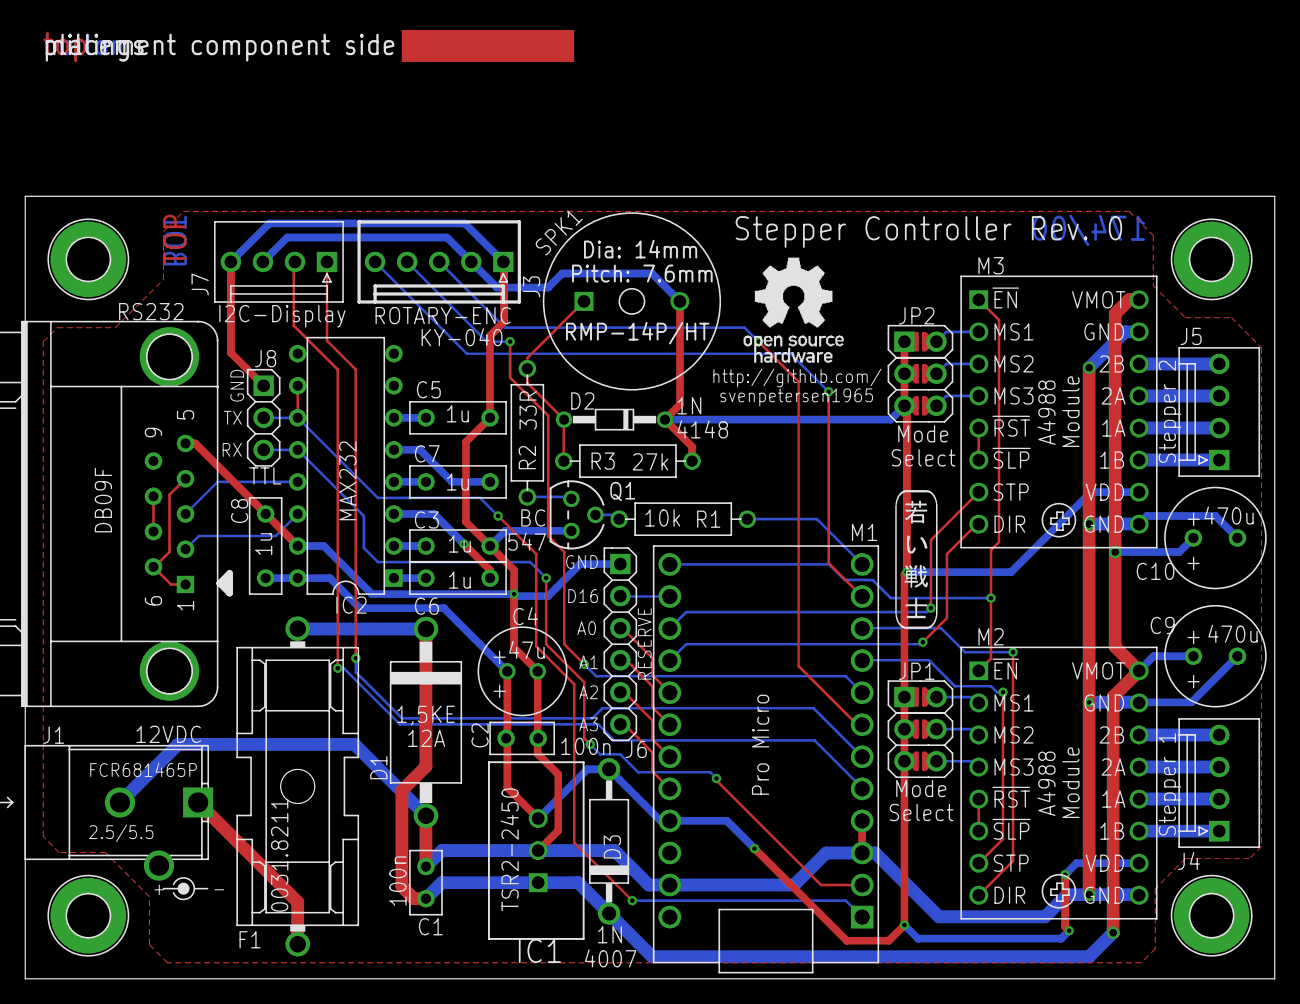
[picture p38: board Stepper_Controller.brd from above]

Board: 2 copper layers, 99.0 x 62.0 mm, 42 parts (0 on the bottom side), 51 nets.

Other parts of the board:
U$59: PCB-TITLE/
U$71: SVEN_TAG
U$77: 2LAYER

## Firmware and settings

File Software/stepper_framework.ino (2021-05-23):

#include <Wire.h>                   // import Wire library 
#include <LiquidCrystal_I2C.h>      // import LiquidCrystal_I2C library


// Pin definitions
#define step1 6                    // stepper 1 step
#define dir1 7                     // stepper 1 direction
#define step2 14                   // stepper 2 step
#define dir2 15                    // stepper 2 direction
#define nstpena 10                 // enable both steppers (active low) 

#define rot_sw 4                   // rotary encoder switch
#define rot_data 5                 // rotary encoder data
#define rot_clk 8                  // rotary encoder clock

#define buzzer 9                   // buzzer

#define t1_ticks_sec 2016          // the timer1 interrupt occures 2016 times per second
#define debounce 4                 // debouncing the rotary encoder
#define default_step 15            // one step every 10 timer1 interrupts
#define puls_width 30              // pulse width in µs of the step pulse

// directions
#define step_cw HIGH               // for clockwise, the direction pin is HIGH
#define step_ccw LOW               // for counter-clockwise, the direction pin is LOW
#define step_cha 0                      // stepper at channel A
#define step_chb 1                      // stepper at channel B

// state machine states
#define sm_stop 0                  // assigning a numbers to the state machine states
#define sm_set 1
#define sm_run 2

volatile boolean tick_1s = 0;                   // this flag is set every 1sec by the timer1 ISR
volatile boolean step_flag = 0;                 // this flag is set, after the time for the next step elapsed
volatile int step_ticks = 0;                    // the tick counter for the step
volatile int t1_ticks = 0;                      // counts the timer1 interrupts 
volatile int step_duration = default_step;      // full steps are used. This variables knows 

// the rotary encoder is processed by the timer1 ISR
volatile int rot_value = 0;                     // rotary encoder clockwise => value > 0; ccw => value < 0 
volatile boolean rot_button = false;            // true if button is pressed            

// variables for processing the rotary encoder
boolean rot_clk_status = HIGH;
boolean rot_clk_status_old = HIGH;
boolean rot_read;
int rot_clk_debounce = debounce;
int rot_sw_debounce = debounce;
boolean rot_sw_status = HIGH;
boolean rot_sw_status_old = HIGH;

boolean st_direction = step_cw;                // Default: clockwise
long num_steps = 0;                            // number of steps
int stepper=step_cha;                          // selects the stepper motor  

char recByte;
String recString = "";                        // receive command buffer
volatile boolean recComplete = false;
boolean syntaxError;

int state_machine;                             // this variable holds the state of the state machine 

LiquidCrystal_I2C lcd(0x27, 16, 2);            // define the lcd display (i²c address 0x27, 16 columns, 2 lines

// ****************************************
// * this is the heartbeat of the system! *
// ****************************************

ISR(TIMER1_COMPA_vect) { // function which will be called when an interrupt occurs at timer 1
  // every one second
  if (++t1_ticks == t1_ticks_sec) {   // set tick_1s every 2000 IRQ cycles (every 1 second)
    tick_1s = 1;                       
    t1_ticks = 0;                     // reset the tick counter
  }

  // count the time before te next steppper step
  if (++step_ticks == step_duration) {
    step_flag = 1;
    step_ticks = 0;
  }
  
  // ============== rotary encoder ==================
  rot_read = digitalRead( rot_clk ); 
  if ( rot_read != rot_clk_status) {              // is rot_clk different for <debounce> cycles?
    if (--rot_clk_debounce == 0) {              
      rot_clk_status = rot_read;                  // if yes: change status
    }
  }
  else {
    rot_clk_debounce = debounce;                  // if it is equal -> reset the debounce counter
  }
  if (rot_clk_status != rot_clk_status_old) {     // did a status change occur?
     if (rot_clk_status == LOW) {                 // is it a falling edge?
       if (digitalRead( rot_data ) == LOW) {      // yes: set the roraty value according to rot_data
         rot_value--;                             // LOW -> CCW
       }
       else {
         rot_value++;                             // HIGH -> CW
       }
     }
     rot_clk_status_old = rot_clk_status;         // update old status
  }
  rot_read = digitalRead( rot_sw );               // read rot switch
  if ( rot_read != rot_sw_status) {               // is rot_sw different for <debounce> cycles?
    if (--rot_sw_debounce == 0) {              
      rot_sw_status = rot_read;                   // if yes: change status
    }
  }
  else {
    rot_sw_debounce = debounce;                    // if it is equal -> reset the debounce counter
  }
  if (rot_sw_status != rot_sw_status_old) {       // did a status change occur?
     if (rot_sw_status == LOW) {                  // is it a falling edge?
       rot_button = true;                         // set switch semaphore
     }
     rot_sw_status_old = rot_sw_status;           // update old status
  }
}

// some functions
void start_screen(void) {                        // display the starte message on the LCD display
  lcd.clear();
  lcd.setCursor(0,0); 
  lcd.print("Stepper Cntr.");
}

void stop_screen(void) {
  lcd.clear();                        // clear the display
  lcd.setCursor(0,0);                 // position the cursor left, top
  lcd.print("Stop=>Channel ");        // Ausgabe: Stop
  if (stepper == step_cha) {
    lcd.print("A");
  }
  else {
    lcd.print("B");
  }
  lcd.setCursor(0,1);
  lcd.print("Steps: ");
  lcd.print( num_steps );
}

void run_screen(void) {
  lcd.clear();                                     // clear the LCD display
  lcd.setCursor(0,0);                                
  lcd.print("Run");                                // print state "Run" on screen
  lcd.noBlink();
  lcd.setCursor(0,1);
}

void makeStepA( void ) {                        // make a step on motor A
  digitalWrite( step1, HIGH );
  delayMicroseconds( puls_width );
  digitalWrite( step1, LOW );
}

void makeStepB( void ) {                        // make a step on motor B
  digitalWrite( step2, HIGH );
  delayMicroseconds( puls_width );
  digitalWrite( step2, LOW );
} 


// This function is called once at start up. It initializes the system
void setup() {
   /* ==================== TIMER 1 setup ======================= */
  // Interrupt every 0.000496 sec (= 2016.13Hz) 
  // prescaler = 256
  // Compare Match Register = 30

  cli(); // disable interrupts  
  // reset timer1 
  TCCR1A = 0;                          // set TCCR1A register to 0
  TCCR1B = 0;                          // set TCCR1B register to 0
  TCNT1  = 0;                          // reset counter value

  OCR1A = 30;                          // set compare match register of timer 1
  
  TCCR1B |= (1 << CS12);               // 1:256 prescaling for timer1  

  TCCR1B |= (1 << WGM12);              // turn on CTC mode
  TIMSK1 |= (1 << OCIE1A);             // enable timer compare interrupt

  sei();                               // allow interrupts
  
  lcd.begin(); //Im Setup wird der LCD gestartet (anders als beim einfachen LCD Modul ohne 16,2 in den Klammern denn das wurde vorher festgelegt
  start_screen();                      // initial display

  Serial1.begin(9600);                 // the RS232 interface (RX, TX on pin 0 and 1) is Serial1. 
  Serial1.println( "Hello RS-232" );   // say hello
  
  // setup stepper controller
  digitalWrite( step1, LOW );                // LOW -> Step Signal 
  digitalWrite( dir1,  st_direction  );      // default direction 
  digitalWrite( step2, LOW );                // LOW -> Step Signal 
  digitalWrite( dir2, st_direction );        // default direction 
  
  digitalWrite( nstpena, HIGH );             // disable stepper by setting the enable pin HIGH
  
  pinMode( step1, OUTPUT );                  // step1 is an output
  pinMode( dir1, OUTPUT );                   // dir1 is an output
  pinMode( step2, OUTPUT );                  // step1 is an output
  pinMode( dir2, OUTPUT );                   // dir1 is an output
  pinMode( nstpena, OUTPUT );                // nstpena is an output, that is the enable output for both stepper controlelrs

  pinMode(rot_sw, INPUT_PULLUP);             // rotary encoder: all signals input with pull-up
  pinMode(rot_data, INPUT_PULLUP);
  pinMode(rot_clk, INPUT_PULLUP);

  pinMode( buzzer, OUTPUT );                // the buzzer is an output

  recString.reserve(80);

  // beep "hello"
  tone( buzzer, 4000 );               // 1kz sound on buzzer
  delay( 1000 );                      // for 1 second
  noTone( buzzer ); 
  
  // state machine
  state_machine =  sm_run;           // first state is "run"
  // initialize the LCD display
  lcd.backlight();                    // backlight on
  switch (state_machine) {
    case sm_stop : {
      stop_screen();
      lcd.blink();
      break;   
    }
    case sm_run : {
      run_screen();
      lcd.noBlink();
      digitalWrite( dir1,  st_direction  ); 
      digitalWrite( dir2,  st_direction  ); 
      digitalWrite( nstpena, LOW );                    // enable stepper controller
      step_ticks = 0;                                  // reset flags
      step_flag = 0;
      break;   
    }
  }
  // reset rotary encoder variables (again) 
  rot_value = 0;                      // reset rot_value
  rot_button = false;                 // reset button semaphore
}

// this is being executed on incoming data over Serial1
void serialEvent1() {
  while (Serial1.available()) {       // bytes available on Serial1?
    recByte = (char)Serial1.read();   // read it
    if (recByte == (char)10) {        // is it "new line character"?
      recComplete = true;             // yes: the line is complete
    }
    else {
      recString += recByte;           // no: append character to input string
    }
  }
}

void loop() {
  // state machine
  switch (state_machine) {
    // state: stop =============================================================================================
    case sm_stop : {                                       // STOP
        lcd.setCursor(14,0);
        if (rot_button==true) {                            // rotary encoder: button pushed
          rot_button = false;                              // reset this flag  after detection                            
          Serial1.print("Button->set (Channel ");
          if (stepper == step_cha) {
            Serial1.println("A)");
          }
          else {
            Serial1.println("B)");
          }
          num_steps = 0;
          state_machine = sm_set;                          // change to state "set"
        }
        if (rot_value != 0) {
          if (rot_value < 0) {
            stepper=step_cha;
            lcd.print("A");
          }
          else {
            stepper=step_chb;
            lcd.print("B");
          }
          rot_value = 0;
        }
        break;
    } // sm_stop
    // state: set =============================================================================================
    case sm_set : {                                       // SET
        lcd.setCursor(7,1);
        if (rot_button==true) {                            // rotary encoder: button pushed
          rot_button = false;                              // reset this flag  after detection                            
          run_screen();
          Serial1.println("Button->run");
          if (num_steps<0) {
            num_steps = -num_steps;
            st_direction = step_ccw;
          }
          else {
            st_direction = step_cw; 
          }
          digitalWrite( dir1,  st_direction  ); 
          digitalWrite( dir2,  st_direction  ); 
          digitalWrite( nstpena, LOW );                    // enable stepper controller
          tone( buzzer, 4000 );                            // 1kz sound on buzzer
          delay( 300 );                                    // for 0.3 second
          noTone( buzzer );
          step_ticks = 0;                                  // reset flags
          step_flag = 0;
          state_machine = sm_run;                          // change to state "run"
        }
        if (rot_value != 0) {
           if (rot_value < 0) {
             num_steps = num_steps - 10;
             rot_value++;
           }
           else {
             num_steps = num_steps + 10;
             rot_value--;
           }
           lcd.setCursor(7,1);
           lcd.print( num_steps );
           lcd.print( "  " );
           Serial1.print( "Steps: " );
           Serial1.println( num_steps );
        }
        break;
    }
    // state: run =============================================================================================
    case sm_run : {
        if (step_flag == 1) {
          step_flag = 0;
          if (num_steps > 0) {
            if (stepper == step_cha) {
               makeStepA();  
            }
            else {
              makeStepB();
            }
            num_steps--;
          }
        }
        if (rot_button==true) {
          rot_button = false;                 
          stop_screen();
          lcd.blink();
          Serial1.println("Button->stop");
          digitalWrite( nstpena, HIGH );                   // disable stepper controller
          tone( buzzer, 4000 );                            // 1kz sound on buzzer
          delay( 300 );                                    // for 0.3 second
          noTone( buzzer );
          state_machine = sm_stop;
        }
        if (recComplete) {                                 // a complete command line is received on RS-232 
            lcd.setCursor(0,1);                            // position the cursor on the second line
            lcd.print( recString );                        // print the received string
            lcd.print( "               " );                // clear the line after that string
            
            // now parsing the command line
            recString.toUpperCase();                       // convert the line to upper case (it is not case sensitive)
            syntaxError = false;                           // reset the Syntax Error flag
            
            if (recString[0] == 'A') {                     // is the first character an A?
              stepper = step_cha;                          // yes: select Stepper#1 (channel A)
            }
            else  if (recString[0] == 'B') {               // is the first character a B?
              stepper = step_chb;                          // yes: select Stepper#2 (channel B)
            }
            else {
              syntaxError = true;                          // else, the syntax is not correct.
            }
            if (!syntaxError) {                            // syntax still correct?
              int pos = (int) recString.indexOf(",");      // find the first comma ","
              if (pos < 1) {                               // if no comma is found
                syntaxError = true;                        // set the Syntax Error Flag
              }
              else {                                       // a comma is found:
                recString.remove(0,pos+1);                 // remove the beginning, the comma included
                num_steps = (int) recString.toInt();       // convert the string to integer -> num_steps
                if (num_steps<0) {                         // is it a negative number?
                   num_steps = -num_steps;                 // yes: make it positive
                   st_direction = step_ccw;                //      the direction is counterclockwise
                }
                else {                                     // no:
                  st_direction = step_cw;                  // the direction is clockwise
                }
                digitalWrite( dir1,  st_direction  );      // set the direction of both stepper motors
                digitalWrite( dir2,  st_direction  ); 
              }
            }
            if (syntaxError) {
              Serial1.println("? SYNTAX ERROR");           // report the syntax error
            }
            else {
              Serial1.print("Execute: Channel ");          // report the execution
              switch (stepper) {
                case step_cha: {
                  Serial1.print("A, ");                    // Channel A
                  break;
                }
                case step_chb: {
                  Serial1.print("B, ");                    // Channel B
                  break;
                }
              }
              Serial1.print( num_steps );                  // and the number of steps
              if (st_direction == step_cw) {
                Serial1.println(" steps, CW");             // and the direction
              }
              else {
                Serial1.println(" steps, CCW");
              }
            }
            recComplete = false;                           // reset the semaphore
            recString = "";                                // reset the recString (receive buffer)
        }
        break;
    } // sm_run
  } // switch (state_machine)
} // loop                        
